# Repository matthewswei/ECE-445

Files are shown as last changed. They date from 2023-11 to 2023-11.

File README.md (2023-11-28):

# UIUC ECE 445

Senior Design Project Laboratory by UIUC. This repository contains all the documents, files, and code used for Fall 2023 Team 2's project (Ground-Breaking Next-Gen Smart Pet Door). For more information on the project, read the design document inside the repo.

## Team Members

Jeffrey Deng

Norbert Szczotka

Matthew Wei

## TA

Abhisheka Mathur Sekar

## File Information

**Design Document.pdf:** Design document containing all the details about our project

**ECE 445 Proposal.pdf:** Project proposal containing the initial planning and ideas

**Lab Notebook.pdf:** Lab notebook containing weekly updates and progress

**Senior Design RFA:** Initial project approval document

**Team Contract Fulfillment.pdf:** Team contract fulfillment document

**Team Contract.pdf:** Team contract outlying rules

**application.py:** User application code

**camera.c:** Camera module code

**ece445final.kicad_pcb:** PCB layout file for final design

**ece445final.kicad_sch:** Schematic file for final design

**esp32.c:** ESP32 microcontroller code

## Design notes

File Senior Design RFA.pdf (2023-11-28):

Ground-Breaking Next-Gen Smart Pet Door

Team Members:
- Norbert Szczotka (nszczo2)
- Jeffrey Deng (jdeng13)
- Matthew Wei (mswei2)

Problem Statement

Have you ever had to leave work or school to let your dog outside? Have you ever needed to pay dog-sitters and give them access to your home? Introducing the ground-breaking Next-Gen Smart Pet Door, which is designed to convenience both pets and their owners when it comes to technology and pet care. This project specifically aims to create a pet door which opens and closes based on motion-detection through real-time camera monitoring viewed through our own smartphone app. Pet owners have full access in giving their loved ones the ability to roam freely remotely. The app includes full functionality of the door, which gives users the ability to open and close the door based on the display of the camera.

Solution

As described in our problem statement, it will provide customers with a pet door that allows the users to open it remotely. At a high level, our design will revolve around modifying an existing door to fit our dog door. This dog door is controlled by the user through a phone app. Subsystems of this design include the app, the door, the sensors, the power system, and the camera. Motion detectors will be used to alert the customer when the pet is near the door and needs to enter. A camera will also be used to prevent unwanted visitors or other animals from entering. The door will close after some time has passed to prevent the door from being always open. In addition, the app can also be used to manually cancel the door open and close it immediately. This system will be on both sides of the door, so the pet can get in and out and not be trapped outside.

Solution Components

### 1. Sensor

This subsystem is the part of our design that senses movement and feeds live video. Once the sensors get triggered, a notification will be sent to the app and the cameras will start sending live feed as well. We will need sensors for motion detection, cameras for live feed, and a wireless transmitter to feed video to the app for the owner to see.

### 2. Door

This subsystem will be the mechanical side of our project. It will involve a stepper motor connected to a simple rolling pulley system that we will design. It will be a small version of the actual product and will be bolted onto a piece of plywood to demonstrate its functionality. It will have an opening and closing function.

### 3. User App

This subsystem contains the controls for the door. It will receive the video feed from the cameras as well as send out controls to the door to open and close when necessary. This part of the project will be entirely software based and will go off of the wireless transmitter on the other subsystems to send and receive the required signals.

### 4. Camera

The camera will be activated from the microcontroller to send a live feed locally to a laptop which will in turn upload to our application. This allows us to workaround the limitations of cheap pcb scale cameras.

### 5. Power Supply

Our power supply system will include a high-quality 12V battery specifically for its capacity and stability for power. To meet the demands of other subsystems, we will need to incorporate voltage regulation techniques to control and stabilize the output voltage based on load conditions. Our design will use step-down voltage regulators for our microcontroller to minimize power flowing through to avoid damage.

Criterion For Success

For the end of our project, we expect the project to be fully functional. We need to make sure the sensor can accurately detect motion and alert the camera to turn it on. This alert must also be able to send a signal to our app and feed the camera feed to the app.The app from here must be able to work properly (buttons and camera). The button when pressed should be able to successfully send a signal to the door and cause it to open. The door should be able to close after a certain amount of time has passed on its own and stop the camera feed from being sent to the app. This same criteria should be applied to the other side of the door as well. Once all these functions are working properly, then we can determine the project is effective.

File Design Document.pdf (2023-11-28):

# ECE 445

### Fall 2023

Senior Project Design Document

# Ground-Breaking Next-Gen Smart Pet Door

Team 2
Jeffrey Deng
Norbert Szczotka
Matthew Wei
September 28, 2023
TA: Abhisheka Mathur Sekar

## 1. Introduction

### 1.1 Problem and Solution

Have you ever had to leave work or school to let your dog outside? Have you ever needed to pay dog-sitters and give them access to your home? Introducing the ground-breaking Next-Gen Smart Pet Door, which is designed to convenience both pets and their owners when it comes to technology and pet care. This project specifically aims to create a pet door which opens and closes based on motion-detection through real-time camera monitoring viewed through our own smartphone app. Pet owners have full access in giving their loved ones the ability to roam freely remotely. The app includes full functionality of the door, which gives users the ability to open and close the door based on the display of the camera.

As described in our problem statement, it will provide customers with a pet door that allows the users to open it remotely. At a high level, our design will revolve around modifying an existing door to fit our dog door. This dog door is controlled by the user through a phone app. Subsystems of this design include the app, the door, the sensors, the power system, and the camera. Motion detectors will be used to alert the customer when the pet is near the door and needs to enter. A camera will also be used to prevent unwanted visitors or other animals from entering. The door will close after some time has passed to prevent the door from being always open. This system will be on both sides of the door, so the pet can get in and out and not be trapped outside.

### 1.2 Visual Aid

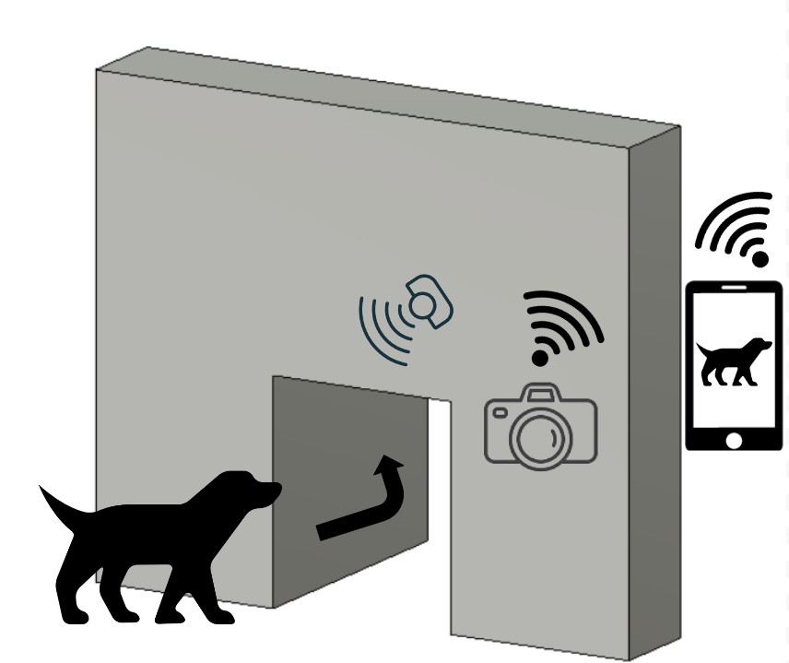
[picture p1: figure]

Figure 1: Visual View of Project

### 1.3 High-level requirements list

1. Sensors are able to detect motion on both sides of the wall and are able to power on the camera within 5 seconds. Camera will remain on for said duration as long as the pet is detected within the scope of the sensor’s field. Camera also must be able to connect to wifi and stream proper video to be extracted for the app’s use.
2. The user app must be able to communicate with the motors sending and receiving signals between the 2 systems within 2 seconds. The user will be able to make the decision to open or close the door via the application by monitoring the camera feed that displays the location of their pet.
3. The door should be able to open and close within 5 seconds in order to prevent the pet from waiting too long to enter or other unwanted guests to come into the house after opening. This door design should be sturdy enough to handle any pets that hit or bump the door while waiting for the door to open or while passing through. The door also has a failsafe in case a pet takes too long to pass through the door and the door tries to close while the pet is inside the frame.

## 2. Design

### 2.1 Block Diagram

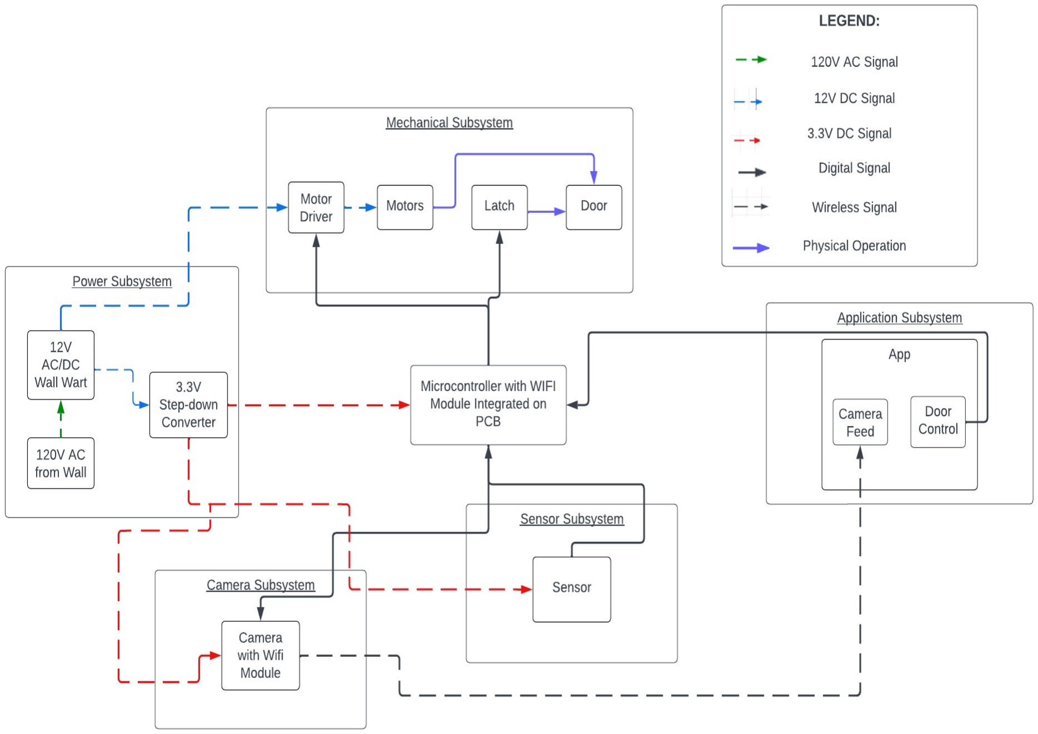
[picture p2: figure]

Figure 2: Control Flow of Design

### 2.2 Physical Design (if applicable)

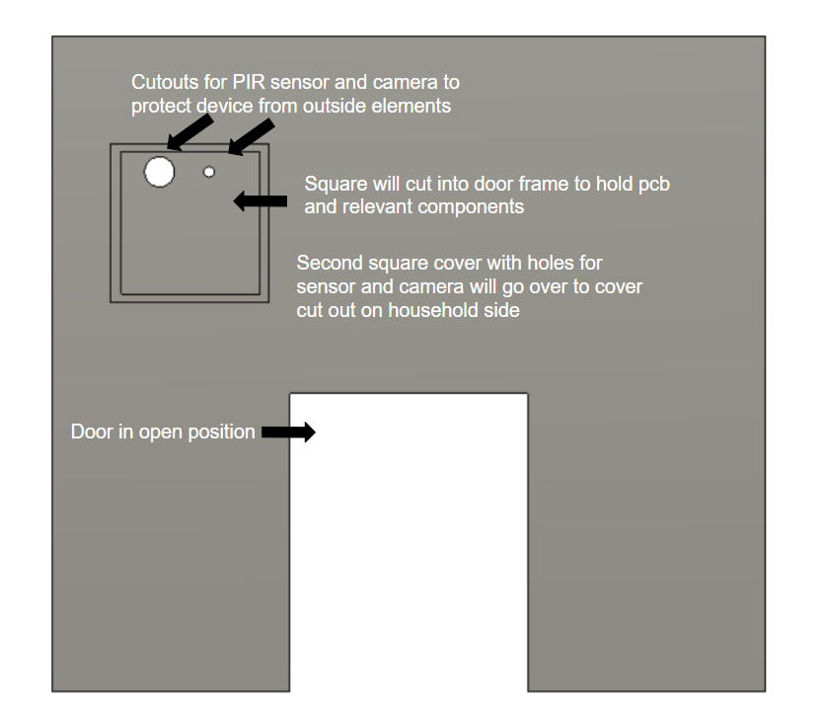
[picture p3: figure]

Figure 3: Door Front View

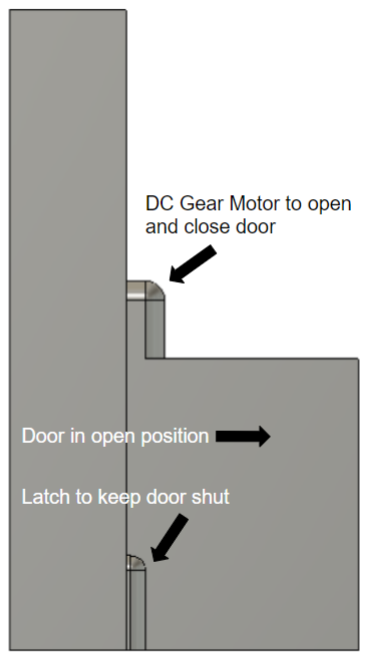
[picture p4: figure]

Figure 4: Door Side View

### 2.3 Camera Subsystem

The camera will be activated from the microcontroller to send a live feed locally to a laptop which will in turn upload to our application. This allows us to workaround the limitations of cheap pcb scale cameras. Our door consists of two cameras: one will be positioned on the inside while the other will be positioned on the outside. We will be using the ESP32 Cam system to transmit feed to the app through a wifi connection module

Requirements | Verification
Camera turn on when sensor detects heat | Trigger sensor and verify camera response is what we need
Camera feed correctly sends video wirelessly | See if video is obtainable on software side

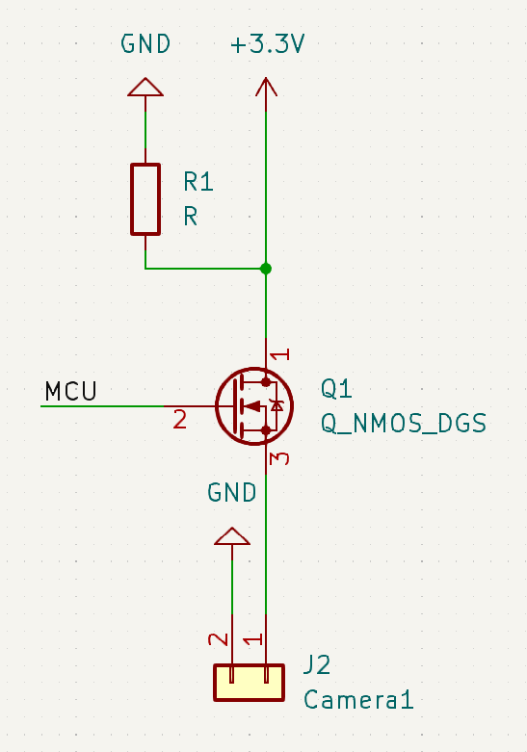
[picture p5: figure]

Figure 5: Camera Basic Design

### 2.4 Mechanical Subsystem

This subsystem will be the mechanical side of our project. It will involve a DC gear motor connected to a swinging door system that we will design. It will be a small version of the actual product and will be bolted onto a piece of plywood to demonstrate its functionality. It will have an opening and closing function. We plan to use a DC motor with a quad encoder which allows the motor to operate forward and reversed in order to open and close the door. In addition to the motor, we will have a solenoid latch to prevent unwanted door openings from either side of the door.

Requirements | Verification
Motors correctly can spin both directions | See if the door opens and closes properly by sending a signal to the quad encoder. High signal to A input should rotate clockwise and high signal to B input should rotate

| counter-clockwise.
Latch functions properly | Push on the door to try to force the door open while the latch is engaged. If it remains closed then we confirm functionality.
Motors correctly receive signal from Wireless module to spin both directions | Test on app with open and closing and seeing if it reflects on the motors action

### 2.5 Power Supply Subsystem

Our power supply system will include a Chanzon 12V 1A 12W Power Supply Charger AC DC Switching Adapter (Input 100-240V, Output 12 Volt 1 Amp) Wall Wart Transformer specifically for its stability for power and accessibility to be connected to a wall outlet. To meet the demands of other subsystems, we will also need to incorporate voltage regulation techniques to control and stabilize the input voltage based on load conditions. Our design will use step-down voltage regulators in the form of integrated circuit chips for our microcontroller to minimize power flowing through to avoid damage.

Two different IC chips will be used: one that steps down 12V to 3.3V to connect to our microcontroller and another that converts 12V to 5V to connect to our camera and sensors. These ICs will utilize decoupling circuits with capacitors for stable circuit operation and The motor will use the unregulated voltage of 12V directly from the wall wart. The wall wart will connect to these voltage regulators via a 12V DC Power Connector 5.5mm x 2.1mm, CENTROPOWER Power Jack Adapter to make the output of the wall wart, which is a barrel connector into a jumper cable, which is then able to be soldered onto the PCB, which will have the ICs already integrated on it.

Requirement | Verification
The power system must be able to supply 3.3V to the microcontroller and 5V to the camera/PIR sensor and 12V to the motor. | Must use a 12V 1A 12W Power Supply Charger AC DC Switching Adapter (Input 100-240V, Output 12 Volt 1 Amp) Wall Wart Transformer to convert the voltage from the wall outlet into 3.3V and 5V. 12V will be directly connected in order to supply our motors. Utilize a voltmeter with the triple output DC power supply to confirm voltage after conversion to make sure it meets the requirements of the microcontroller, camera, and PIR sensor.

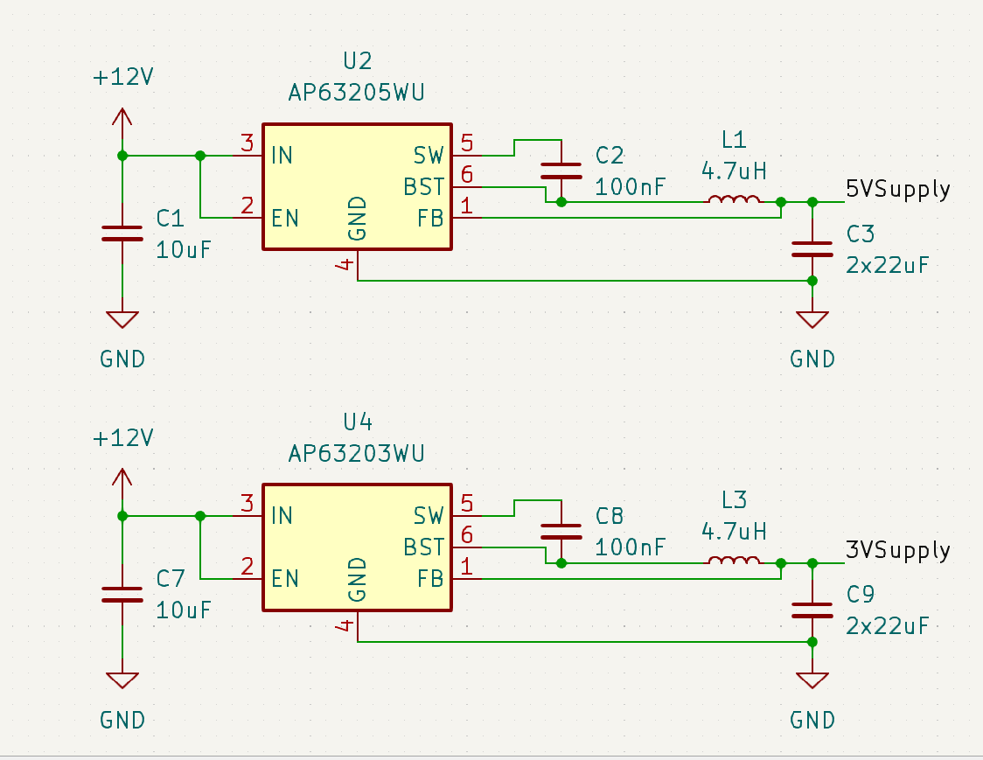
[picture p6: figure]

Figure 6: Power Supply Basic Design

### 2.6 Sensor Subsystem

This subsystem is the part of our design that senses movement and feeds live video. The system will use 2 HiLetgo AM312 Mini Pyroelectric PIR Detectors. Once the sensors get triggered, a notification will be sent to the app and the cameras will start sending live feed as well. When it is detected that the sensor is high, a signal will be sent to the microcontroller, where it will be processed by logic to send a signal to turn the camera on. We will need sensors for motion detection, cameras for live feed, and a wireless transmitter to send video to the app for the owner to see.

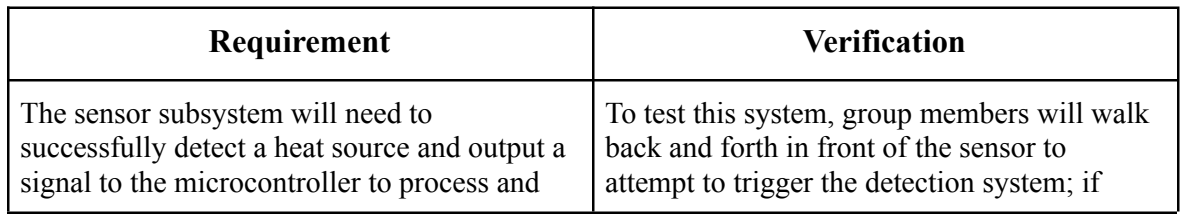
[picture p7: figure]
Requirement; Verification; The sensor subsystem will need to

successfully detect a heat source and output a signal to the microcontroller to process and

To test this system, group members will walk back and forth in front of the sensor to attempt to trigger the detection system; if

activate the camera. | functioning properly, we will be able to record a signal from the oscilloscope. Additional testing includes the delay time of the sensor. Confirming it is indeed 2 seconds will help prevent false triggers such as the dog just passing by instead of waiting at the door.

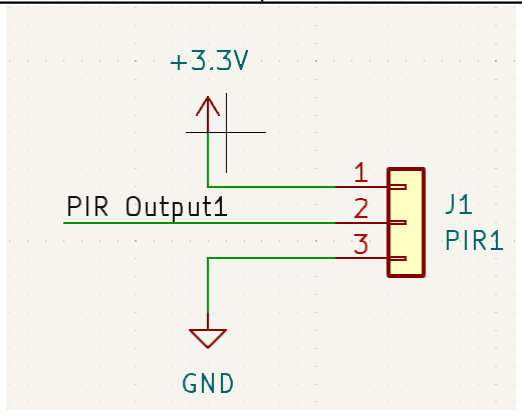
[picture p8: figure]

Figure 7: Sensor Basic Design

### 2.7 User App System

This subsystem contains the controls for the door. It will receive the video feed from the cameras as well as send out controls to the door to open and close when necessary. This part of the project will be entirely software based and will go off of the wireless transmitter on the other subsystems to send and receive the required signals. The app will need a connection to the wifi module in order to communicate with the camera subsystem on the same local network. From there, the wifi module will transmit data so the camera feed and door control will be available.

Requirements | Verification
App has all required buttons and overlays available | Make sure there is a spot for video feed from camera and make sure open and close button is available Done through visual verification and testing if open and close button work properly on software side
App compiles properly and logic works | Make sure the app is complete with working logic. Can be done with test cases and seeing if specific input and outputs match with each

other.

App correctly receives signal from camera | Check for correct live video feed from the camera. This can be tested by seeing if video can be shown on the app.
App correctly receives signal from microcontroller | Check for a signal received originating from the sensor to trigger camera on. This can be tested on the software side by adding test cases to see if anything is picked up.
App correctly sends signal to microcontroller | Check if a signal from the hardware side is received. This can be tested with an oscilloscope to see if the signal is sent properly

### 2.8 Tolerance Analysis

In our design, we utilize PIR sensors to detect the animal and activate the camera system to transmit live feed to the phone application. However, there is an intrinsic flaw in the PIR sensor design. While its range of seven meters is sufficient for our uses, the field of sensing is only 100 degrees. This means that when the animal is close and off to either side of the sensor it might not be able to detect them. This can be solved with overlapping sensor fields that cover each other's blindspots. We need to make sure that the angle we point them at sufficiently covers this.

Another issue we could run into is insufficient current delivery. We are using a wall wart that supplies 1A to the system. The ESP32 microcontroller has a minimum load requirement of 0.5A, the PIR sensors each use 0.1mA, the two cameras use 40mA each. This totals to less than 1A so we should be fine to use this wall wart.

Another key factor is the power and heat generated from our voltage regulation techniques. The wall wart AC/DC converter outputs 12.05-12.18V at low load, and 11.81-11.97V at full load. The current will be 1A. Thus, Ptmax = 12.18V * 1A = 12.18W, and Ptmin = 11.81 * 1A = 11.81W. Next, according to Figure 8, the 3.3V voltage regulator operates at a 90% efficiency at Vin = 12V and Vout = 3.3V. So, Pvrmax = Pin * (1 - eff) = (12V * 1A) * (1-0.9) = 1.2W.

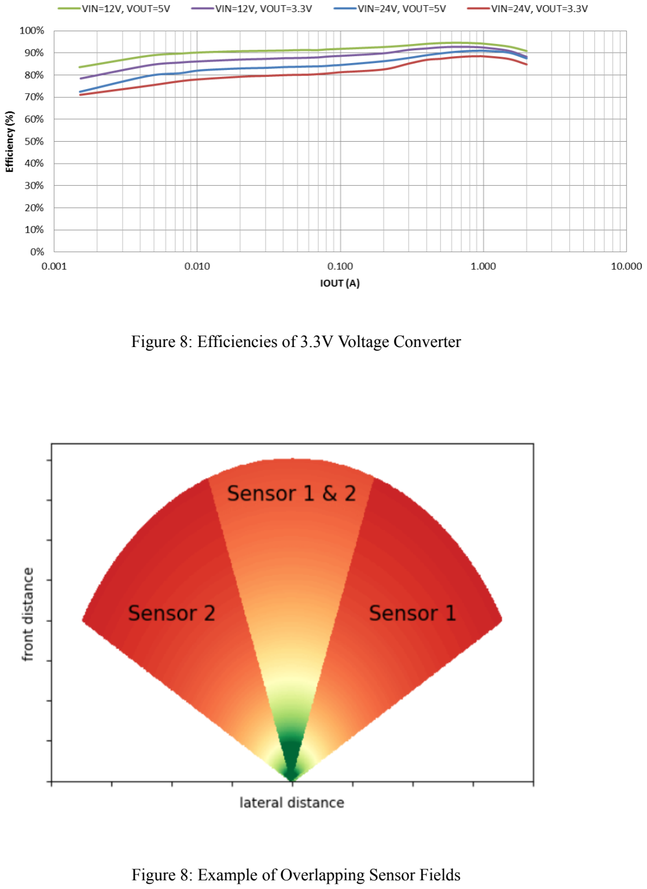
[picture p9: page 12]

Figure 8: Efficiencies of 3.3V Voltage Converter

Figure 8: Example of Overlapping Sensor Fields

## 3. Cost and Schedule

### 3.1 Cost Analysis

Quanti ty | Part | Part Number | Manufacturer | Total Cost ($) | Part Link
1 | DC gear motor | N/A | BBQ Driver | 14.88 | Link (https://www.amazon.com/Encoder-Metal-Gearmotor-Arduino-Printers/dp/B07GNG6S2H?s=industrial)
1 | Solenoid lock | A19042500ux0016 | uxcell | 15.49 | Link (https://www.amazon.com/uxcell-Electromagnetic-Solenoid-Assembly-Electirc/dp/B07TMWY94C)
3 | PIR sensor | AM312 | HiLetgo | 8.69 | Link (https://www.amazon.com/HiLetgo-Pyroelectric-Sensor-Infrared-Detector/dp/B07RT7MK7C)
1 | Microcontroller | ESP-WROOM-32 | Aokin | 8.99 | Link (https://www.amazon.com/Aokin-ESP-WROOM-32-Development-Bluetooth-Microcontroller/dp/B08NW77465/?th=1)
2 | Camera | ESP32-CAM | HiLetgo | 18.49 | Link (https://www.amazon.com/HiLetgo-ESP32-CAM-Development-Bluetooth-Raspberry/dp/B07RXPHYNM)
1 | 3.3 V Converter | AP63203WU-7 | Diodes Incorporated | 0.87 | Link (https://www.digikey.com/en/products/detail/diodes-incorporated/AP63203WU-7/9858426)
1 | USB 2.0 to TTL Module Serial Converter Adapter Module USB to TTL Downloader | CP2102 | HiLetgo | 7.39 | Link
1 | H-Bridge Motor Driver for DC Motors | 110300681 | ECE Supply Store | 1.85 | N/A
1 | Wall Power Supply | N/A | Chanzon | 9.99 | Link (https://www.amazon.com/Chanzon-Switching-100-240V-Transformer-Security/dp/B07G1219LQ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)
1 | Female Header | N/A | Centropower | 7.99 | Link (https://www.amazon.com/Power-Connector-Female-Adapter-Camera/dp/B07C61434H?hvadid=366410038949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)
3 | MOSFET N-CH | DMG3402LQ-7 | Diodes Incorporated | 1.32 | Link
1 | 4.7µH Inductor | LQM21DN4R7N0 0D | Murata Electronics | 0.25 | Link
N/A | Miscellaneous Circuit Elements | Resistors, Capacitor, | N/A | 10 | N/A

| | Inductors
Parts total | | | | 106.20
3 | Labor (group) | N/A | N/A | 48,750 | N/A
1 | Labor (machine shop) | N/A | N/A | 880 | N/A
Labor Total | | | | 49,630
Grand Total | | | | 49,736.2

The total cost for parts as seen above including shipping and sales tax is $96.26. We will assume it took us 13 hours per week for 10 weeks. We can expect a salary of $50/hr (approximately the average salary of an electrical engineer in the US) ×2.5 (overhead factor) × 130 hours worked = $16,250 per team member. The total labor cost should account for all 3 members, therefore, $16,250 x 3 = $48,750. Now to account for the labor done by the team in the machine shop, we expect $22/hr for a total of 40 hours spent producing the mechanical design, thus, $22 x 40 = $880. This comes out to be a total cost of $49,736.2.

### 3.2 Schedule

Week | Task | Team Member
9/18 | Begin design document Complete parts list | All
| Begin structuring app | Matthew
| Look into PCB and microcontroller requirements | Norbert
| Finish 3D model for machine shop and review with Greg | Jeffrey
9/25 | Finish design document Finalize PCB design | All
| Work on app development | Matthew
| Supervise hardware and software design to ensure correctness Order all necessary parts and components | Norbert
| Check with machine shop on mechanical design and make any adjustments necessary Assist in PCB design | Jeffrey
10/2 | Design review with instructor and TA PCB review | All
| App must be nearing completion. Testing not required at this point since we will need to wait for PCB to come in | Matthew
| Ensure PCB design meets all requirements based on our subsystems | Norbert
| Finalize mechanical design with machine shop to begin build | Jeffrey
10/9 | Program the microcontroller Order PCB | All
| Ensure software is programmed to take care of every scenario possible based on user demands | Matthew
| Responsible for making sure PCB is able to communicate with software on the app as well as the mechanical design | Norbert
| Work on integrating PCB with the mechanical subsystem from the finalized product from machine shop | Jeffrey
10/16 | Begin testing PCB with a breadboard/prototype design | All

| Identify weak/strength points in current PCB design | Matthew
| Document progress and begin data collection | Norbert
| Visualize how the PCB can be integrated better with mechanical design | Jeffrey
10/23 | Begin integrating PCB with mechanical design as well as all subsystems | All
| Ensure app can communicate with WIFI module on PCB | Matthew
| Search for optimizing design, look for weak points and assist with integration and verification of subsystem connections | Norbert
| Begin mounting subsystems on mechanical design | Jeffrey
10/30 | Carry out testing of product | All
| Ensure electrical connections are proper | Matthew
| Assist in both mechanical/electrical verification | Norbert
| Ensure mechanical design is proper | Jeffrey
11/6 | Continue testing and making adjustments of product | All
| Data collection | Matthew
| Document all technical information related to performance of design | Norbert
| Verify that performance of product matches data | Jeffrey
11/13 | Mock demo | All
| Prepare for mock demo | Matthew
| Prepare for mock demo, ensure requirements are met | Norbert
| Prepare for mock demo, transport final product | Jeffrey
11/20 | Fall break | All
| Catch up on work | Matthew
| Catch up on work | Norbert
| Catch up on work | Jeffrey

## 4. Discussion of Ethics and Safety

When considering ethics and safety, the safety of the pet is the number one concern as its intended design is to assist animals from entering and leaving an area. The main concerns that arose were animal injuries and interactions with the door, exposure of the electronics to outside factors, and potential leakage in power. The design will be enclosed to prevent the electronics from being exposed to outside factors like water and power will be monitored during the design process to make sure everything is within its required range. The animal’s injuries and interactions with the door will also be handled during the design phase. This will be done by choosing a specific door which will be strong enough to avoid damage from the animal and the motor rate will be weak and slow enough to prevent injuries to the animal. Also, there will be an additional sensor by the door to prevent the door from shutting all the way in case the pet is in the door area when the door is closing. This will prevent the pet from being squished within the door. The inclusion of the camera in our design also will prevent wild animals or unwanted guests from entering as it will allow the owner to see what is at the door.

According to the IEEE Code of Ethics I, the design needs to have high standards and value human ethics and behavior. As addressed in the paragraph above, the issues regarding safety, health, and welfare have been resolved and considered. Concerning privacy and conflicts of interest, we will honestly disclose any information and usage of data to affected parties. Unprofessional activities will also be avoided to maintain the moral code of the team. Criticism of the design will also be acknowledged and considered as we believe no design is perfect and improvements can always be made. Essentially, the team will always be willing to learn and take in advice.

11/27 | Prepare final demo for instructor and TA | All
| Carryout final demo | Matthew
| Carryout final demo | Norbert
| Carryout final demo | Jeffrey
12/4 | Prepare for final presentation for instructor and TA Return lab equipment | All
| Present final presentation Turn in Lab Notebook with Github | Matthew
| Present final presentation | Norbert
| Present final presentation | Jeffrey

According to the IEEE Code of Ethics II and III, all persons in the team and outside the team will be treated equally and without discrimination. No harassment shall be allowed and this will be upheld by the team members being accountable with each other. To avoid injuries, all members of the team have taken the Lab Safety Training and know how to be responsible in the lab. Additionally, two people will be in the room at the same time to watch each other incase of an emergency. Finally, we will ensure each of the team members will keep each other in check with the ethics. We shall strive to ensure the code is upheld and report to higher-ups when not complied.

## 5. Citations

“IEEE Code of Ethics.” IEEE, https://www.ieee.org/about/corporate/governance/p7-8.html.

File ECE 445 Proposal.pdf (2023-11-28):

# ECE 445

### Fall 2023

Senior Design Project Proposal

# Ground-Breaking Next-Gen Smart Pet Door

Team 2
Jeffrey Deng
Norbert Szczotka
Matthew Wei
September 10, 2023
TA: Abhisheka Mathur Sekar

# Table of Contents

### I. Introduction

1. Problem
2. Solution
3. Visual Aid
4. High-level requirements list

### II. Design

1. Block Diagram
2. Subsystem Overview
i. Camera
ii. Mechanical
iii. Power Supply
iv. Sensor
v. User App
3. Subsystem Requirements
4. Tolerance Analysis

### III. Ethics and Safety

### IV. References

## 1. Introduction

### 1.1 Problem

Have you ever had to leave work or school to let your dog outside? Have you ever needed to pay dog-sitters and give them access to your home? Introducing the ground-breaking Next-Gen Smart Pet Door, which is designed to convenience both pets and their owners when it comes to technology and pet care. This project specifically aims to create a pet door which opens and closes based on motion-detection through real-time camera monitoring viewed through our own smartphone app. Pet owners have full access in giving their loved ones the ability to roam freely remotely. The app includes full functionality of the door, which gives users the ability to open and close the door based on the display of the camera

### 1.2 Solution

As described in our problem statement, it will provide customers with a pet door that allows the users to open it remotely. At a high level, our design will revolve around modifying an existing door to fit our dog door. This dog door is controlled by the user through a phone app. Subsystems of this design include the app, the door, the sensors, the power system, and the camera. Motion detectors will be used to alert the customer when the pet is near the door and needs to enter. A camera will also be used to prevent unwanted visitors or other animals from entering. The door will close after some time has passed to prevent the door from being always open. This system will be on both sides of the door, so the pet can get in and out and not be trapped outside.

### 1.3 Visual Aid

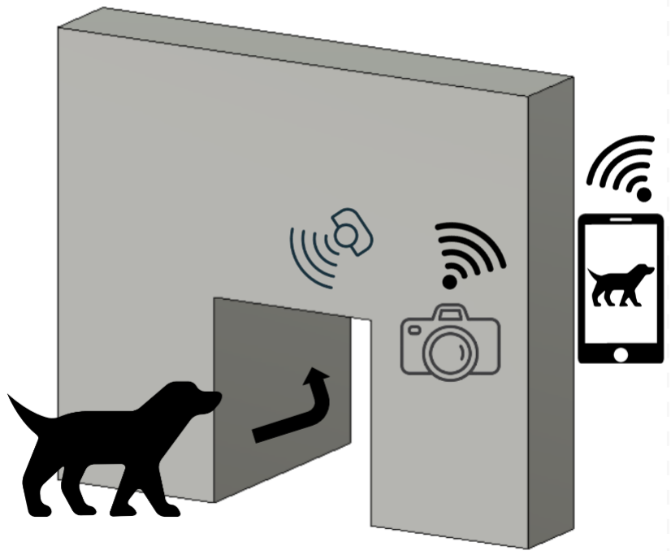
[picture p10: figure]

### 1.4 High-level requirements list

1. Sensors are able to detect motion on both sides of the wall and are able to power on the camera within 5 seconds. Camera will remain on for said duration as long as the pet is detected within the scope of the sensor’s field. Camera also must be able to connect to wifi and stream proper video to be extracted for the app’s use.
2. The user app must be able to communicate with the motors sending and receiving signals between the 2 systems within 2 seconds. The user will be able to make the decision to open or close the door via the application by monitoring the camera feed that displays the location of their pet.

3. The door should be able to open and close within 5 seconds in order to prevent the pet from waiting too long to enter or other unwanted guests to come into the house after opening. This door design should be sturdy enough to handle any pets that hit or bump the door while waiting for the door to open or while passing through. The door also has a failsafe in case a pet takes too long to pass through the door and the door tries to close while the pet is inside the frame.

## 2. Design

2.1 Block Diagram Break your design down into blocks and assign these blocks into subsystems. Label voltages and data connections. Your microcontroller can live in multiple subsystems if you wish, as in the example below.

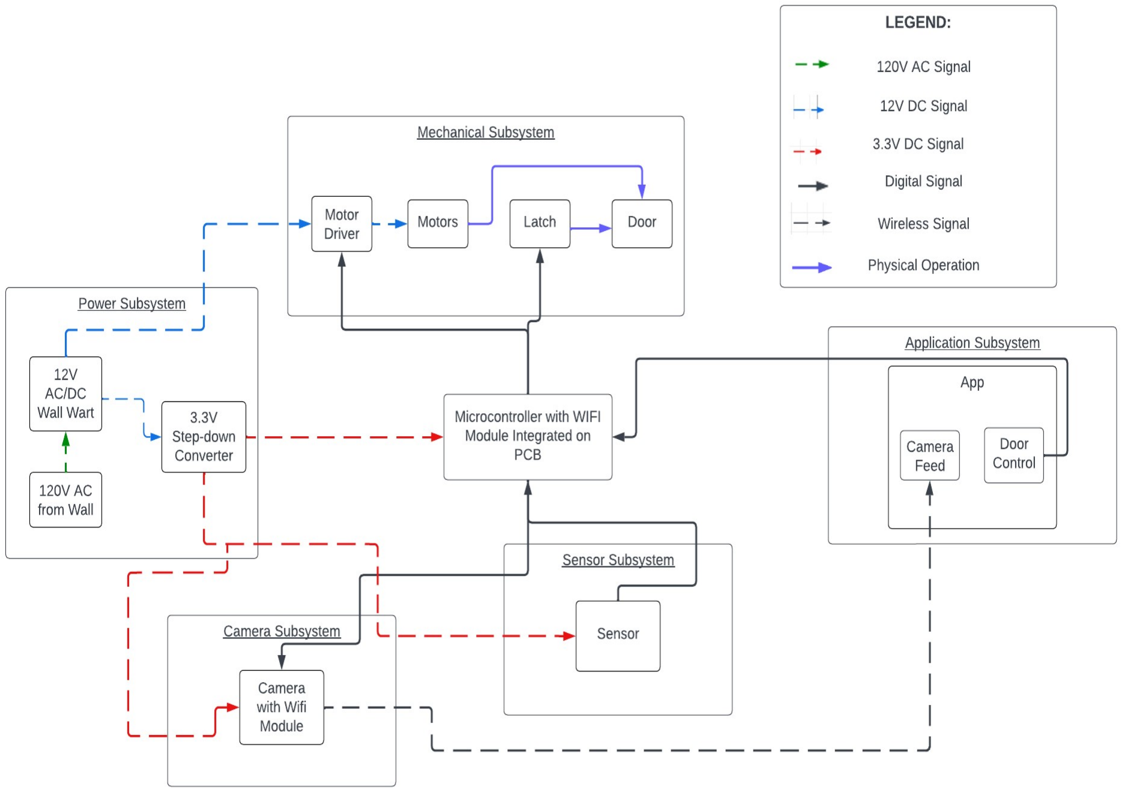
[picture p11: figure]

### 2.2 Subsystem Overview

Camera

The camera will be activated from the microcontroller to send a live feed locally to a laptop which will in turn upload to our application. This allows us to workaround the limitations of cheap pcb scale cameras. Our door consists of two cameras: one will be positioned on the inside while the other will be positioned on the outside. We will be using the ESP32 Cam system to transmit feed to the app through a wifi connection module.

Mechanical

This subsystem will be the mechanical side of our project. It will involve a DC gear motor connected to a swinging door system that we will design. It will be a small version of the actual product and will be bolted onto a piece of plywood to demonstrate its functionality. It will have an opening and closing function. We plan to use a DC motor with a quad encoder connected to the motor driver that acts as an H-bridge, which allows the motor to operate forward and reversed in order to open and close the door. In addition to the motor, we will have a solenoid latch to prevent unwanted door openings from either side of the door.

Power Supply

Our power supply system will include a Chanzon 12V 1A 12W Power Supply Charger AC DC Switching Adapter (Input 100-240V, Output 12 Volt 1 Amp) Wall Wart Transformer specifically for its stability for power and accessibility to be connected to a wall outlet. The wall wart essentially behaves as a 120V AC to 12V DC converter. To meet the demands of other subsystems, we will also need to incorporate voltage regulation techniques to control and stabilize the input voltage based on load conditions. Our design will use step-down voltage regulators in the form of integrated circuit chips for our microcontroller to minimize power flowing through to avoid damage.

A voltage regulator will be used to step down 12V to 3.3V to connect to our microcontroller, camera, and sensors. This IC will utilize decoupling circuits with capacitors for stable circuit operation and the motor driver will use the voltage of 12V directly from the wall wart. The wall wart will connect to these voltage regulators via a 12V DC Power Connector 5.5mm x 2.1mm, CENTROPOWER Power Jack Adapter to make the output of the wall wart, which is a barrel connector into a jumper cable, which is then able to be soldered onto the PCB, which will have the ICs already integrated on it.

Sensor

This subsystem is the part of our design that senses movement and feeds live video. The system will use 2 HiLetgo AM312 Mini Pyroelectric PIR Detectors. Once the sensors get triggered, a notification will be sent to the app and the cameras will start sending live feed as well. When it is detected that the sensor is high, a signal will be sent to the microcontroller, where it will be processed by software to send a signal to turn the camera on.

User App

This subsystem contains the controls for the door. It will receive the video feed from the cameras as well as send out controls to the door to open and close when necessary. This part of the project will be entirely software based and will go off of the wireless transmitter on the other subsystems to send and receive the required signals. The app will need a connection to the wifi module in order to communicate with the camera subsystem on the same local network. From there, the wifi module will transmit data so the camera feed and door control will be available.

### 2.3 Subsystem Requirements

Camera

We will have two requirements for this subsystem: Camera must turn on when sensor detects heat, and camera feed correctly sends video wirelessly. In order to verify the mentioned requirements, it is necessary to trigger the sensor and verify camera response is what we need, and see if video is obtainable on the software side, respectfully.

Mechanical

One requirement is to ensure motors correctly can spin in both directions. To verify this we must see if the door opens and closes properly by sending a signal to and from the motor driver. High signal to A input should rotate clockwise and high signal to B input should rotate counter-clockwise. We also require that the latch functions properly, which will be verified by pushing on the door to try to force the door open while the latch is engaged. If it remains closed then we confirm functionality. The final requirement is that the motors correctly receive signal from wireless module to spin both directions. This will be confirmed by testing on app with open and closing and seeing if it reflects on the motors action.

Power Supply

A requirement of the power system is to be able to supply 3.3V to the microcontroller, camera, PIR sensor and 12V to the motor driver. Must use a 12V 1A 12W Power Supply Charger AC DC Switching Adapter (Input 100-240V, Output 12 Volt 1 Amp) Wall Wart Transformer to convert the voltage from the wall outlet into 3.3V. 12V will be directly connected to the motor driver in order to supply our motors. We can verify this by utilizing a voltmeter with the triple output DC power supply in the lab to confirm voltage after conversion to make sure it meets the requirements of the microcontroller, camera, and PIR sensor.

Sensor

The sensor subsystem will need to successfully detect a heat source and output a signal to the microcontroller to process and activate the camera. To test this system, group members will walk back and forth in front of the sensor to attempt to trigger the detection system; if functioning properly, we will be able to record a signal from the oscilloscope. Additional testing includes the delay time of the sensor. Confirming it is indeed 2 seconds will help prevent false triggers such as the dog just passing by instead of waiting at the door.

User App

The app has all required buttons, overlays available, and compiles properly with how our logic works. It also needs to correctly receive live feed from the two cameras. Finally it needs to correctly send and receive signals to and from the microcontroller

### 2.4 Tolerance Analysis

In our design, we utilize PIR sensors to detect the animal and activate the camera system to transmit live feed to the phone application. However, there is an intrinsic flaw in the PIR sensor design. While its range of seven meters is sufficient for our uses, the field of sensing is only 100 degrees. This means that when the animal is close and off to either side of the sensor it might not be able to detect them. This can be solved with overlapping sensor fields that cover each other's blindspots. We need to make sure that the angle we point them at sufficiently covers this.

Another issue we could run into is insufficient current delivery. We are using a wall wart that supplies 1A to the system. The ESP32 microcontroller has a minimum load requirement of 0.5A, the PIR sensors each use 0.1mA, the two cameras use 40mA each. This totals to less than 1A so we should be fine to use this wall wart.

## 3. Ethics and Safety

When considering ethics and safety, the safety of the pet is the number one concern as its intended design is to assist animals from entering and leaving an area. The main concerns that arose were animal injuries and interactions with the door, exposure of the electronics to outside factors, and potential leakage in power. The design will be enclosed to prevent the electronics from being exposed to outside factors like water and power will be monitored during the design process to make sure everything is within its required range. The animal’s injuries and interactions with the door will also be handled during the design phase. This will be done by choosing a specific door which will be strong enough to avoid damage from the animal and the motor rate will be weak and slow enough to prevent injuries to the animal. Also, there will be an additional sensor by the door to prevent the door from shutting all the way in case the pet is in the door area when the door is closing. This will prevent the pet from being squished within the door. The inclusion of the camera in our design also will prevent wild animals or unwanted guests from entering as it will allow the owner to see what is at the door.

According to the IEEE Code of Ethics I, the design needs to have high standards and value human ethics and behavior. As addressed in the paragraph above, the issues regarding safety, health, and welfare have been resolved and considered. Concerning privacy and conflicts of interest, we will honestly disclose any information and usage of data to affected parties. Unprofessional activities will also be avoided to maintain the moral code of the team. Criticism of the design will also be acknowledged and considered as we believe no design is perfect and improvements can always be made. Essentially, the team will always be willing to learn and take in advice.

According to the IEEE Code of Ethics II and III, all persons in the team and outside the team will be treated equally and without discrimination. No harassment shall be allowed and this will be upheld by the team members being accountable with each other. To avoid injuries, all members of the team have taken the Lab Safety Training and know how to be responsible in the lab. Additionally, two people will be in the room at the same time to watch each other incase of an emergency. Finally, we will ensure each of the team members will keep each other in check with the ethics. We shall strive to ensure the code is upheld and report to higher-ups when not complied.

## 4. Reference

“IEEE Code of Ethics.” IEEE, https://www.ieee.org/about/corporate/governance/p7-8.html.

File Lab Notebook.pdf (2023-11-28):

# ECE 445

### Fall 2023

Weekly Semester Lab Notebook

# Ground-Breaking Next-Gen Smart Pet Door

Team 2
Jeffrey Deng
Norbert Szczotka
Matthew Wei
TA: Abhisheka Mathur Sekar

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

| Search for optimizing design, look for weak points and assist with integration and verification of subsystem connections | Norbert
| Begin mounting subsystems on mechanical design | Jeffrey
10/30 | Carry out testing of product | All
| Ensure electrical connections are proper | Matthew
| Assist in both mechanical/electrical verification | Norbert
| Ensure mechanical design is proper | Jeffrey
11/6 | Continue testing and making adjustments of product | All
| Data collection | Matthew
| Document all technical information related to performance of design | Norbert
| Verify that performance of product matches data | Jeffrey
11/13 | Mock demo | All
| Prepare for mock demo | Matthew
| Prepare for mock demo, ensure requirements are met | Norbert
| Prepare for mock demo, transport final product | Jeffrey
11/20 | Fall break | All
| Catch up on work | Matthew
| Catch up on work | Norbert
| Catch up on work | Jeffrey
11/27 | Prepare final demo for instructor and TA | All
| Carryout final demo | Matthew
| Carryout final demo | Norbert
| Carryout final demo | Jeffrey
12/4 | Prepare for final presentation for instructor and TA Return lab equipment | All
| Present final presentation Turn in Lab Notebook with Github | Matthew
| Present final presentation | Norbert
| Present final presentation | Jeffrey

## Weekly Updates and Notes

Week of 9/18
- On schedule
- Worked on design doc and project proposal
- Started to get basic idea on how project should be built as well as the logic and control flow

Week of 9/25
- Behind schedule
- Worked on design doc
- Drew out schematic of how the circuit should be built
- Ordered parts

Week of 10/2
- Behind schedule
- Design review
- Worked on project proposal rewrite
- Ordered parts
- Layout for PCB
- First round PCB layout done

Week of 10/9
- Behind schedule
- Ordered parts
- Reworked logic in schematic (found errors)
- Second round PCB layout done
- Worked on team work evaluation
- Unit tested components (sensor, motor driver, H-bridge, ESP32 dev board) in lab
- Started camera code
- Finished same day
- Tested camera code and camera by itself
- Worked first try and effortlessly
- Could not connect to Illinois WiFi or hotspot
- Demo at home?

Week of 10/16
- Behind schedule
- Worked on design documentation rewrite
- Ordered parts
- Reworked logic in schematic (found errors)
- Third round PCB layout done

Week of 10/23
- Behind schedule
- Worked on individual progress report
- Ordered parts
- Added microcontroller programming buttons in schematic (forgot to do)
- Fourth round PCB layout done

Week of 10/30
- Got on schedule
- Microcontroller code and application code has started being written
- Finished same week
- Tried to compile microcontroller
- Had issues with pins not working as intended
- Changed pin variable to “const int” and it worked

Week of 11/6
- On schedule
- Tested PIR sensor with MOSFET and camera
- Not working, voltage not high enough
- When voltage is high, camera takes a long time to turn on
- Changed some logic and now works
- Tested sensor with microcontroller code
- Worked flawlessly
- Tested motor and door with microcontroller code
- Opened and closed, but sometimes didn’t close all the way
- Small adjustment to timers to make it work
- Most subsystems work (only need to test wireless open/close button on app)

Week of 11/13
- On schedule
- Wireless webserver code started being written
- Finished same day

- Tested wireless webserver code with app and door
- Worked effortlessly
- Tested camera with MOSFET for turn on after sensor detection
- Worked, but camera takes as long time to turn on
- All subsystems officially working as intended on breadboard
- Worked on team contract fulfillment
- Did mock demo
- Soldered components onto PCB
- Microcontroller not getting programmed properly
- Sent door into machine shop to include a box to hold PCB and other components
- Can now connect to Illinois WiFi

Week of 11/20
- No work done (Thanksgiving break)

Week of 11/27
- On schedule
- Soldered development board onto PCB as a work around
- Tested every subsystem and verified it is working
- Power converter stopped working day before demo
- Found another workaround for power
- Did final demo
- Started to work on final report
- Started to work on final presentation
- Did mock final presentation

Week of 12/5
- On schedule
- Final presentation
- Worked on final report

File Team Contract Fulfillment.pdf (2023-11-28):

Norbert Szczotka, Jeffrey Deng, Matthew Wei

Team #2

Team Contract Fulfillment

Project Goals: This section should begin with a short description of what you planned on building at the start of the

semester. What were the goals of your project? You should elaborate on whether these goals were met.

At a high level, our design will revolve around modifying an existing door to fit our dog door. This dog door is

controlled by the user through an app. Subsystems of this design include the app, the door, the sensors, mechanical,

the power system, and the camera. Motion detectors will be used to alert the customer when the pet is near the door

and needs to enter. A camera will also be used to prevent unwanted visitors or other animals from entering. In

addition, the app can also be used to manually open the door and close it immediately. This system will be on both

sides of the door, so the pet can get in and out and not be trapped outside.

For the end of our project, we expect the project to be fully functional by the time of the final demo. We need to

make sure the sensor can accurately detect motion and alert the camera to turn it on. This alert must also be able to

send a signal to our app and feed the camera footage to the app. The app from here must be able to work properly

(buttons and camera). The button when pressed should be able to successfully send a signal to the door and cause it

to open. This same criteria should be applied to the other side of the door as well. Once all these functions are

working properly, then we can determine the project is effective.

Expectations: This section should address whether the expectations set in the “Expectations” section in your team

contract were met. Essentially, were the ground rules your team set out at the start of the semester followed?

Our group successfully met the project expectations. Members successfully offered constructive feedback while

ensuring high-quality work. All team members came prepared to meetings and held accountability for their tasks.

We worked together to problem solve and assist each other.

Roles: At the beginning of the course, your team outlined roles as part of the team contract. Please describe what

your roles are now and–if your roles changed–how they evolved as the semester progressed. Did you assign a

leader? Were pieces of the project tackled as a group or individually? Why?

The roles of our team were maintained. We delegated tasks based on individual strengths and weaknesses. Matthew

mostly focused on the software of our microcontroller and app, while Jeffrey worked on the mechanical related

design as well as the PCB orders. Norbert worked on designing various subsystems, technical writing, part selection,

and bridging the gap between software and hardware.

Agenda: How did your team make decisions about the project? How were goals set? When an issue with the project

came up, how did your team plan to fix it?

We made decisions on the project together as a team, where we each had a say in design related choices. At the

beginning of each week, we determined the agenda and for what needs to be accomplished in order to stay on track.

In order to stick to our schedule, we communicated plans through our group chat. When an issue arose, we met

together to discuss possible solutions while coming to a reasonable conclusion.

Team Issues: This section should cover team-related issues that your group encountered during the course. What

sort of problems did you run into? How were they dealt with? Was the process set out in the team contract followed?

In hindsight could you have done things differently to have a better team experience?

Overall, our team did not run into many team related issues over the course of this project so far. The only issues we

had were related to coordination. Occasionally we had conflicting schedules so it was difficult at points to get all of

us together for a meeting. We each put in the work that we had laid out originally in the team contract. While the

pace of work done could have been improved since we are cutting it close to the final deadline. Flexibility also

would have been more helpful.

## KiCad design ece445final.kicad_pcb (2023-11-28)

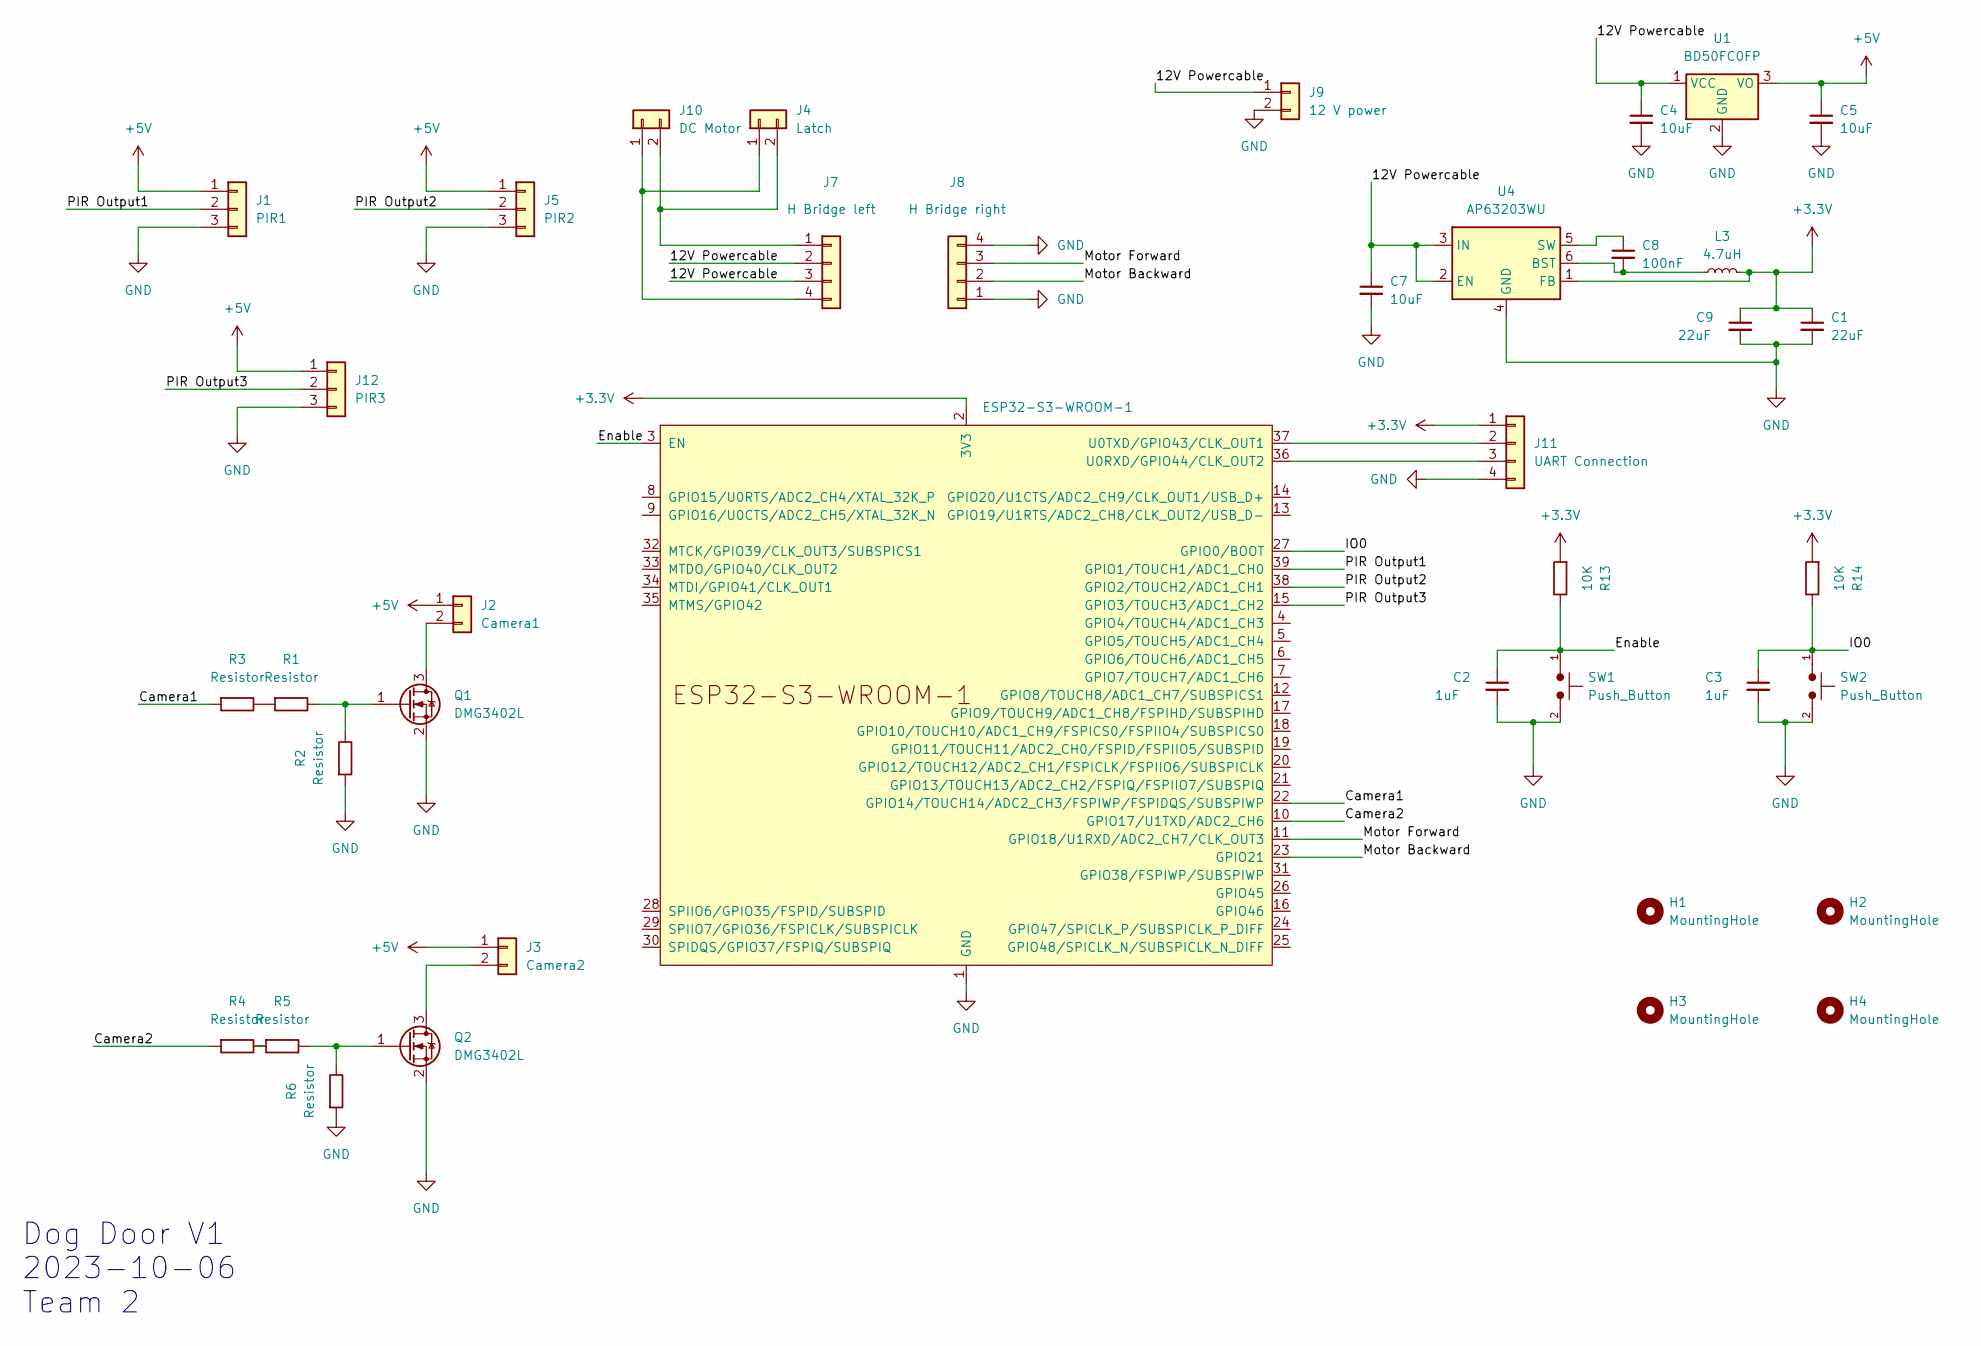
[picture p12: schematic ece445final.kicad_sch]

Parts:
C1, C9: 22uF; C_0805_2012Metric_Pad1.18x1.45mm_HandSolder
C2, C3: 1uF; C_0805_2012Metric_Pad1.18x1.45mm_HandSolder
C4, C5, C7: 10uF; C_0805_2012Metric_Pad1.18x1.45mm_HandSolder
C8: 100nF; C_0805_2012Metric_Pad1.18x1.45mm_HandSolder
H1, H2, H3, H4: MountingHole; MountingHole_3.2mm_M3
J1: PIR1; Molex_KK-254_AE-6410-03A_1x03_P2.54mm_Vertical
J2: Camera1; Molex_KK-254_AE-6410-02A_1x02_P2.54mm_Vertical
J3: Camera2; Molex_KK-254_AE-6410-02A_1x02_P2.54mm_Vertical
J4: Latch; Molex_KK-254_AE-6410-02A_1x02_P2.54mm_Vertical
J5: PIR2; Molex_KK-254_AE-6410-03A_1x03_P2.54mm_Vertical
J7: H Bridge left; Molex_KK-254_AE-6410-04A_1x04_P2.54mm_Vertical
J8: H Bridge right; Molex_KK-254_AE-6410-04A_1x04_P2.54mm_Vertical
J9: 12 V power; Molex_KK-254_AE-6410-02A_1x02_P2.54mm_Vertical
J10: DC Motor; Molex_KK-254_AE-6410-02A_1x02_P2.54mm_Vertical
J11: UART Connection; Molex_KK-254_AE-6410-04A_1x04_P2.54mm_Vertical
J12: PIR3; Molex_KK-254_AE-6410-03A_1x03_P2.54mm_Vertical
L3: 4.7uH; L_0805_2012Metric_Pad1.15x1.40mm_HandSolder
Q1, Q2: DMG3402L; SOT-23
R1, R2, R3, R4, R5, R6: Resistor; R_0805_2012Metric_Pad1.20x1.40mm_HandSolder
R13, R14: 10K; R_0805_2012Metric_Pad1.20x1.40mm_HandSolder
SW1, SW2: Push_Button; SW_PUSH_6mm
U1: BD50FC0FP; TO-252-2
U2: ESP32-S3-WROOM-1
U4: AP63203WU; TSOT-23-6

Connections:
+3.3V: C1.1, C9.1, J11.1, L3.2, R13.1, R14.1, U2.2 (3V3), U4.1 (FB)
+5V: C5.1, J1.1, J2.1, J3.1, J5.1, J12.1, U1.3 (VO)
/12V Powercable: C4.1, C7.1, J7.2, J7.3, J9.1, U1.1 (VCC), U4.2 (EN), U4.3 (IN)
/Camera1: R3.1, U2.22 (GPIO14/TOUCH14/ADC2_CH3/FSPIWP/FSPIDQS/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)
/Camera2: R4.1, U2.10 (GPIO17/U1TXD/ADC2_CH6)
/Enable: C2.1, R13.2, SW1.1, U2.3 (EN)
/IO0: C3.1, R14.2, SW2.1, U2.27 (GPIO0/BOOT)
/Motor Backward: J8.2, U2.23 (GPIO21)
/Motor Forward: J8.3, U2.11 (GPIO18/U1RXD/ADC2_CH7/CLK_OUT3)
/PIR Output1: J1.2, U2.39 (GPIO1/TOUCH1/ADC1_CH0)
/PIR Output2: J5.2, U2.38 (GPIO2/TOUCH2/ADC1_CH1)
/PIR Output3: J12.2, U2.15 (GPIO3/TOUCH3/ADC1_CH2)
GND: C1.2, C2.2, C3.2, C4.2, C5.2, C7.2, C9.2, J1.3, J5.3, J8.1, J8.4, J9.2, J11.4, J12.3, Q1.2 (S), Q2.2 (S), R2.1, R6.1, SW1.2, SW2.2, U1.2 (GND), U2.1 (GND), U2.40 (GND), U2.41 (GND), U4.4 (GND)
unnamed: J2.2, Q1.3 (D)
unnamed: J3.2, Q2.3 (D)
unnamed: J4.1, J7.4, J10.1
unnamed: J4.2, J7.1, J10.2
unnamed: J11.2, U2.37 (U0TXD/GPIO43/CLK_OUT1)
unnamed: J11.3, U2.36 (U0RXD/GPIO44/CLK_OUT2)
unnamed: Q1.1 (G), R1.2, R2.2
unnamed: Q2.1 (G), R5.2, R6.2
unnamed: R1.1, R3.2
unnamed: R4.2, R5.1
unnamed: C8.2, L3.1, U4.6 (BST)
unnamed: C8.1, U4.5 (SW)

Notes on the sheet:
Dog Door V1 2023-10-06 Team 2

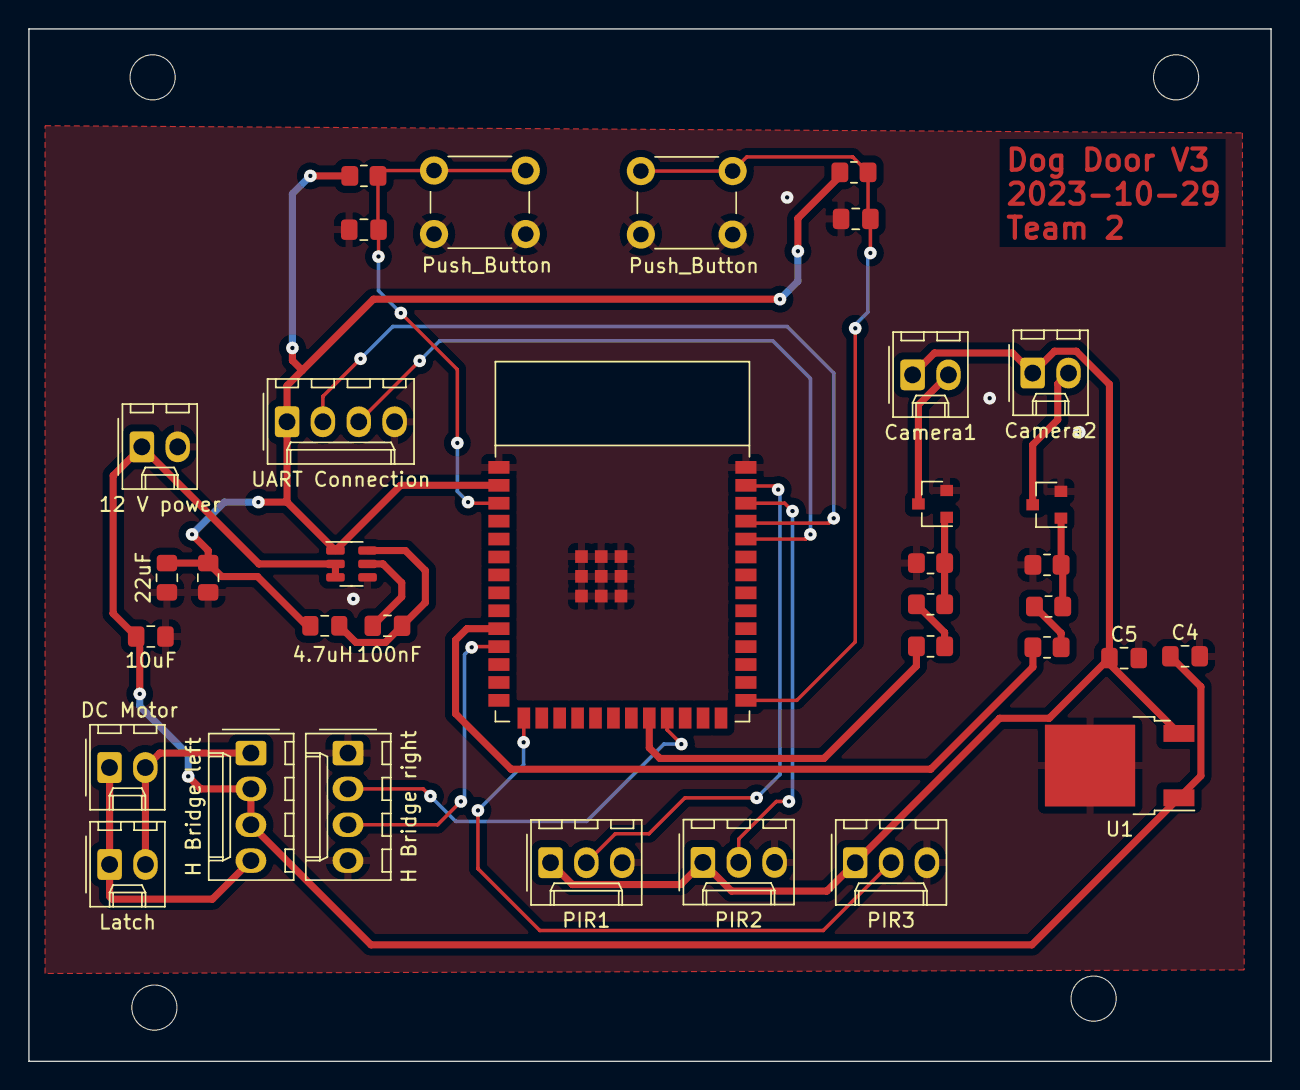
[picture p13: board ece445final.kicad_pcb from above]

Board: 2 copper layers, 88.0 x 73.2 mm, 39 parts (0 on the bottom side), 25 nets.

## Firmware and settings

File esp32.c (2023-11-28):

/*
 * Code for ESP 32 microcontroller for Fall 2023 ECE 445 senior design project.
 *
 * 
 * 
 * 
 * 
 * 
 * 
 * 
 * 
 * 
 * 
 * 
 * 
 * 
 *   https://randomnerdtutorials.com/esp32-async-web-server-espasyncwebserver-library/
 *   https://randomnerdtutorials.com/esp32-client-server-wi-fi/#:~:text=Set%20your%20ESP32%20as%20an,be%20listening%20for%20incoming%20requests.
 * 
*/

#include <WiFi.h>
#include <ESPAsyncWebServer.h>
#include <time.h>
#include <string.h>

// Constants (pins)
const int SENSOR_PIN_1 = 1;  // Sensor input pin 1
const int SENSOR_PIN_2 = 1;  // Sensor input pin 2
const int SENSOR_PIN_3 = 1;  // Sensor input pin 3
const int CAMERA_PIN_1 = 1;  // Camera output pin 1
const int CAMERA_PIN_2 = 1;  // Cmaera output pin 2
const int MOTOR_FWD = 1;  // Motor output pin 1
const int MOTOR_BCK = 1;  // Motor output pin 2
const int BUTTON_PIN = 1; // For testing

// Wifi Connection Information
const char* ssid = "Bring Out The Whole Ocean";
const char* password = "AnotherOne";
AsyncWebServer server(80);

// Global Variables
int SENSOR_EN = 0;
int SENS_TIMER = 0;
int DOOR_EN = 0;
int DOOR_TIMER = 0;
int DOOR_ST = 0;
int SIG_APP = 0;
int prev_time;

/* 
    void setup()

    Set up Wifi, connect the pins properly to each other, setup the timers, pull down/pull up resistors

*/
void setup() {
    Serial.begin(115200);
    Serial.print("Connecting to ");
    Serial.println(ssid);
    WiFi.begin(ssid, password);
    while(WiFi.status() != WL_CONNECTED) {
        delay(500);
        Serial.print(".");
    }
    Serial.println("");
    Serial.print("Connected to WiFi network with IP Address: ");
    Serial.println(WiFi.localIP());

    server.on("/button", HTTP_GET, [](AsyncWebServerRequest *request){
        SIG_APP = 1;
        request->send(200, "text/plain", "pressed"); 
    });

    server.begin();

    pinMode(SENSOR_PIN_1, INPUT);
    pinMode(SENSOR_PIN_2, INPUT);
    pinMode(SENSOR_PIN_3, INPUT);
    pinMode(CAMERA_PIN_1, OUTPUT);
    pinMode(CAMERA_PIN_2, OUTPUT);
    pinMode(MOTOR_FWD, OUTPUT);
    pinMode(MOTOR_BCK, OUTPUT);
    pinMode(BUTTON_PIN, INPUT_PULLUP);

}

/* 
    void loop()

    For pins, 
        - Be able to recieve sensor signal with timer
        - Feed out signal to camera to turn it on
        - Recieve signal from application
        - Turn motors with said signal from appliation
        - Be able to signal if animal is still within door to stop door from closing
        - Signal for latch

*/
void loop() {
    time_t rawtime;
    struct tm* timeinfo;
    time(&rawtime);
    timeinfo = localtime( &rawtime );
    int curr_sec = timeinfo->tm_sec;

    // Check for edge cases (both cameras on)
    if (digitalRead(SENSOR_PIN_1) == HIGH) {
        digitalWrite(CAMERA_PIN_1, HIGH);
        SENS_TIMER = 0;
        SENSOR_EN = 1;
    }
    
    if (digitalRead(SENSOR_PIN_2) == HIGH) {
        digitalWrite(CAMERA_PIN_2, HIGH);
        SENS_TIMER = 0;
        SENSOR_EN = 1;
    }

    // Check if enough time has passed for camera to be turned off
    if (SENS_TIMER==120) {
        digitalWrite(CAMERA_PIN_1, LOW);
        digitalWrite(CAMERA_PIN_2, LOW);
        SENSOR_EN = 0;
    }

    // Get signal from app

    // if (digitalRead(BUTTON_PIN)==HIGH) {
    //     if (DOOR_EN==0) {
    //         DOOR_TIMER = 0;
    //         DOOR_EN = 1;
    //         if (DOOR_ST) {
    //             DOOR_ST = 0;
    //             digitalWrite(MOTOR_FWD, LOW);
    //             digitalWrite(MOTOR_BCK, HIGH);
    //         } else {
    //             DOOR_ST = 1;
    //             digitalWrite(MOTOR_BCK, LOW);
    //             digitalWrite(MOTOR_FWD, HIGH);
    //         }
    //     }
    // }

    if (SIG_APP) {
        if (DOOR_EN==0) {
            DOOR_TIMER = 0;
            DOOR_EN = 1;
            if (DOOR_ST) {
                DOOR_ST = 0;
                digitalWrite(MOTOR_FWD, LOW);
                digitalWrite(MOTOR_BCK, HIGH);
            } else {
                DOOR_ST = 1;
                digitalWrite(MOTOR_BCK, LOW);
                digitalWrite(MOTOR_FWD, HIGH);
            }
        }
        SIG_APP = 0;
    }

    if (DOOR_ST==0) {
        if (DOOR_TIMER==3) {
            DOOR_EN = 0;
            DOOR_TIMER = 0;
            digitalWrite(MOTOR_BCK, LOW);
        }
    } else if (DOOR_ST==1) {
        if (DOOR_TIMER==2) {
            DOOR_EN = 0;
            DOOR_TIMER = 0;
            digitalWrite(MOTOR_FWD, LOW);
        }
    }


    /*
    if (digitalRead(SENSOR_PIN_3) == HIGH) {
        // turn door back, hold door, and reset door timer
    }
    */

    // Increment timers
    if (prev_time==NULL) {
        prev_time = curr_sec;
    } else if (curr_sec!=prev_time) {
        prev_time = curr_sec;
        if (SENSOR_EN) SENS_TIMER++;
        if (DOOR_EN) DOOR_TIMER++;
    }

    // Clear the header variable
    header = "";
    // Close the connection
    client.stop();
    Serial.println("Client disconnected.");
    Serial.println("");
}

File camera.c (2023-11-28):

/*									
 *
 * camera.c - main source file for camera module for Ground-Breaking Next-Gen Smart Pet Door
 *
 * Author:	    Jeffrey Deng
 * Version:	    1.0
 * Creation Date:   Thur Oct  12 2023
 * Filename:	    camera.c
 * History:
 *	Version	1.0
 *		Initial code for camera
 */

#include "esp_camera.h"
#include <WiFi.h>

//
// WARNING!!! PSRAM IC required for UXGA resolution and high JPEG quality
//            Ensure ESP32 Wrover Module or other board with PSRAM is selected
//            Partial images will be transmitted if image exceeds buffer size
//
//            You must select partition scheme from the board menu that has at least 3MB APP space.
//            Face Recognition is DISABLED for ESP32 and ESP32-S2, because it takes up from 15 
//            seconds to process single frame. Face Detection is ENABLED if PSRAM is enabled as well

// ===================
// Select camera model
// ===================
//#define CAMERA_MODEL_WROVER_KIT // Has PSRAM
//#define CAMERA_MODEL_ESP_EYE // Has PSRAM
//#define CAMERA_MODEL_ESP32S3_EYE // Has PSRAM
//#define CAMERA_MODEL_M5STACK_PSRAM // Has PSRAM
//#define CAMERA_MODEL_M5STACK_V2_PSRAM // M5Camera version B Has PSRAM
//#define CAMERA_MODEL_M5STACK_WIDE // Has PSRAM
//#define CAMERA_MODEL_M5STACK_ESP32CAM // No PSRAM
//#define CAMERA_MODEL_M5STACK_UNITCAM // No PSRAM
#define CAMERA_MODEL_AI_THINKER // Has PSRAM
//#define CAMERA_MODEL_TTGO_T_JOURNAL // No PSRAM
//#define CAMERA_MODEL_XIAO_ESP32S3 // Has PSRAM
// ** Espressif Internal Boards **
//#define CAMERA_MODEL_ESP32_CAM_BOARD
//#define CAMERA_MODEL_ESP32S2_CAM_BOARD
//#define CAMERA_MODEL_ESP32S3_CAM_LCD
//#define CAMERA_MODEL_DFRobot_FireBeetle2_ESP32S3 // Has PSRAM
//#define CAMERA_MODEL_DFRobot_Romeo_ESP32S3 // Has PSRAM
#include "camera_pins.h"

// ===========================
// Enter your WiFi credentials
// ===========================
const char* ssid = "IllinoisNet_Guest";
//const char* password = "AnotherOne";

void startCameraServer();
void setupLedFlash(int pin);

void setup() {
  Serial.begin(115200);
  Serial.setDebugOutput(true);
  Serial.println();

  camera_config_t config;
  config.ledc_channel = LEDC_CHANNEL_0;
  config.ledc_timer = LEDC_TIMER_0;
  config.pin_d0 = Y2_GPIO_NUM;
  config.pin_d1 = Y3_GPIO_NUM;
  config.pin_d2 = Y4_GPIO_NUM;
  config.pin_d3 = Y5_GPIO_NUM;
  config.pin_d4 = Y6_GPIO_NUM;
  config.pin_d5 = Y7_GPIO_NUM;
  config.pin_d6 = Y8_GPIO_NUM;
  config.pin_d7 = Y9_GPIO_NUM;
  config.pin_xclk = XCLK_GPIO_NUM;
  config.pin_pclk = PCLK_GPIO_NUM;
  config.pin_vsync = VSYNC_GPIO_NUM;
  config.pin_href = HREF_GPIO_NUM;
  config.pin_sccb_sda = SIOD_GPIO_NUM;
  config.pin_sccb_scl = SIOC_GPIO_NUM;
  config.pin_pwdn = PWDN_GPIO_NUM;
  config.pin_reset = RESET_GPIO_NUM;
  config.xclk_freq_hz = 20000000;
  config.frame_size = FRAMESIZE_UXGA;
  config.pixel_format = PIXFORMAT_JPEG; // for streaming
  //config.pixel_format = PIXFORMAT_RGB565; // for face detection/recognition
  config.grab_mode = CAMERA_GRAB_WHEN_EMPTY;
  config.fb_location = CAMERA_FB_IN_PSRAM;
  config.jpeg_quality = 12;
  config.fb_count = 1;
  
  // if PSRAM IC present, init with UXGA resolution and higher JPEG quality
  //                      for larger pre-allocated frame buffer.
  if(config.pixel_format == PIXFORMAT_JPEG){
    if(psramFound()){
      config.jpeg_quality = 10;
      config.fb_count = 2;
      config.grab_mode = CAMERA_GRAB_LATEST;
    } else {
      // Limit the frame size when PSRAM is not available
      config.frame_size = FRAMESIZE_SVGA;
      config.fb_location = CAMERA_FB_IN_DRAM;
    }
  } else {
    // Best option for face detection/recognition
    config.frame_size = FRAMESIZE_240X240;
#if CONFIG_IDF_TARGET_ESP32S3
    config.fb_count = 2;
#endif
  }

#if defined(CAMERA_MODEL_ESP_EYE)
  pinMode(13, INPUT_PULLUP);
  pinMode(14, INPUT_PULLUP);
#endif

  // camera init
  esp_err_t err = esp_camera_init(&config);
  if (err != ESP_OK) {
    Serial.printf("Camera init failed with error 0x%x", err);
    return;
  }

  sensor_t * s = esp_camera_sensor_get();
  // initial sensors are flipped vertically and colors are a bit saturated
  if (s->id.PID == OV3660_PID) {
    s->set_vflip(s, 1); // flip it back
    s->set_brightness(s, 1); // up the brightness just a bit
    s->set_saturation(s, -2); // lower the saturation
  }
  // drop down frame size for higher initial frame rate
  if(config.pixel_format == PIXFORMAT_JPEG){
    s->set_framesize(s, FRAMESIZE_QVGA);
  }

#if defined(CAMERA_MODEL_M5STACK_WIDE) || defined(CAMERA_MODEL_M5STACK_ESP32CAM)
  s->set_vflip(s, 1);
  s->set_hmirror(s, 1);
#endif

#if defined(CAMERA_MODEL_ESP32S3_EYE)
  s->set_vflip(s, 1);
#endif

// Setup LED FLash if LED pin is defined in camera_pins.h
#if defined(LED_GPIO_NUM)
  setupLedFlash(LED_GPIO_NUM);
#endif

  WiFi.begin(ssid);
  WiFi.setSleep(false);

  while (WiFi.status() != WL_CONNECTED) {
    delay(500);
    Serial.print(".");
  }
  Serial.println("");
  Serial.println("WiFi connected");

  startCameraServer();

  Serial.print("Camera Ready! Use 'http://");
  Serial.print(WiFi.localIP());
  Serial.println("' to connect");
}

void loop() {
  // Do nothing. Everything is done in another task by the web server
  delay(10000);
}
